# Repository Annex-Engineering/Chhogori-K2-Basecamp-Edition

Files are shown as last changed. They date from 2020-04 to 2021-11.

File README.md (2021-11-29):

# Notes:
as of 11-29-2021, K2 Basecamp edition will no longer recieve updates, this was voted upon by the community. We will do our best to make sure all frames are forwards compatible with any XY or Z axis related changes, however, we cannot guarantee anything.
 - Trails

# Chhogori (K2) Printer - Basecamp Edition - Release 2.1

Chhogori (K2) - Basecamp Edition: is a Medium Format, Direct Drive, Open Air FDM Printer.

This is an entirely scratch design, based on the efforts of the "Hypercube Overkill Project" for the XY Motion System

Our discord server can be found here: https://discord.gg/MzTR3zE

BOM/Sourcing Guide for a 250x250x250 Build can be found here: https://docs.google.com/spreadsheets/d/1O3eyVuQ6M4F03MJSDs4Z71_XyNjXL5HFTZr1jsaAtRc/edit?usp=sharing

Frame Calculator: https://docs.google.com/spreadsheets/d/13liXa9Ag0wGGfv0r0511OmAwZuGD7cvcuc0zpDakIw4/edit?usp=sharing

# Stats:
- Open Air Design
- 2020, and 2040 Frame Members
- Build Volumes of ~250^3 to 500^3 (use of whole plate available) + additional area to purge and wipe
     - Z can theoretically be 1m tall, just not fully supported or tested

- Direct Drive Extruder (Sherpa Mini or Ascender)

- Shortest Belt Paths Possible, 4 Motors, 2 Per X, 2 Per Y Axis
- Moving Bed, Fixed Gantry

- MGN12C Rails for XYZ Stationary Rails
- MGN12C Rails with 1515 Backers for XY Cross (Moving Members)
- 12mm 2GT Belts on XY Motion 
- 12mm 2GT Belts with 20 or 40:1 Worm Drive on Z to lift the Bed 
	 - Hybrid Laser Cut Metal and Printed Part Construction
	 - Legacy Support for 15mm 3HTD belts also offered
- Heavy Duty Bearings
- NEMA17 Motors XYZ

- Minimal Printed Parts (ABS or ASA Required)

- Fysetc Spider or S6 Controller + BTT Expander Board with Klipper Required
- Mosquito Style, Dragon Style, Mosquito Magnum+ and Nitram's VolcoMosquito hotends supported
- 24V Power Standard
- Mains Bed

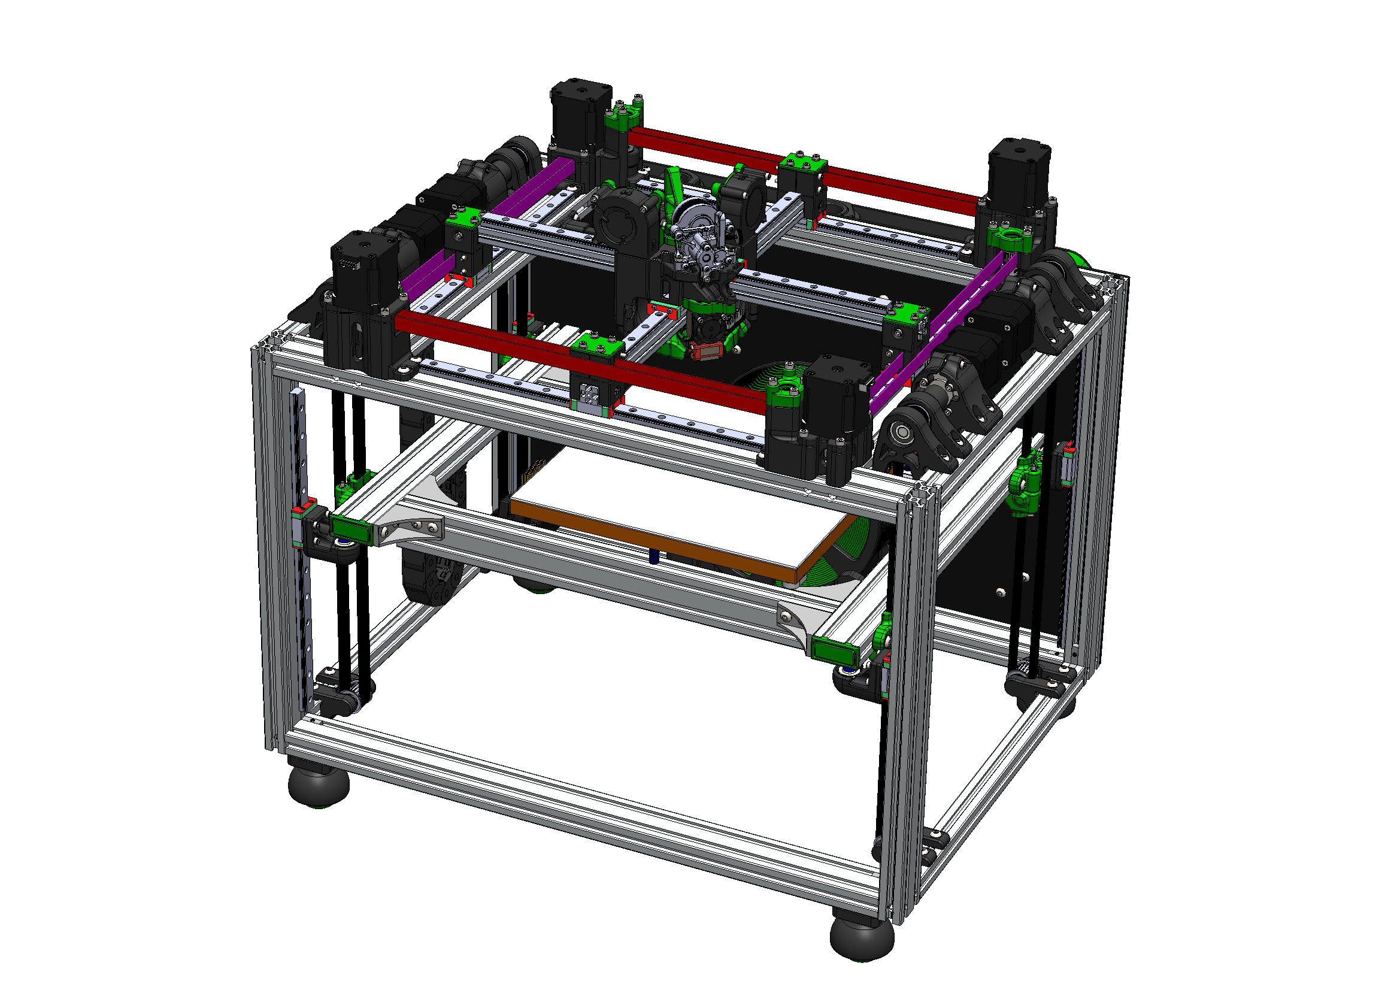
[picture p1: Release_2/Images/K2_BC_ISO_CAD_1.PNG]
Image of Machine with Panels


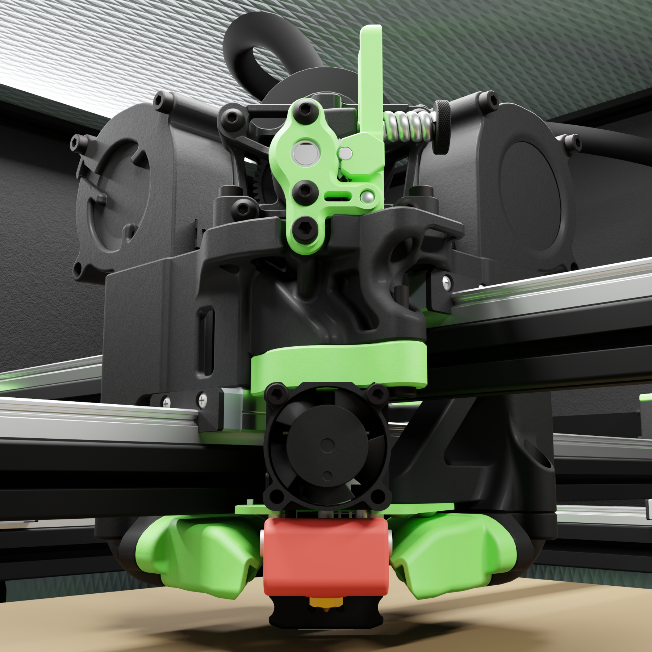
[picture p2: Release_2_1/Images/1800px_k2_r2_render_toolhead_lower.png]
Image of Toolhead 1


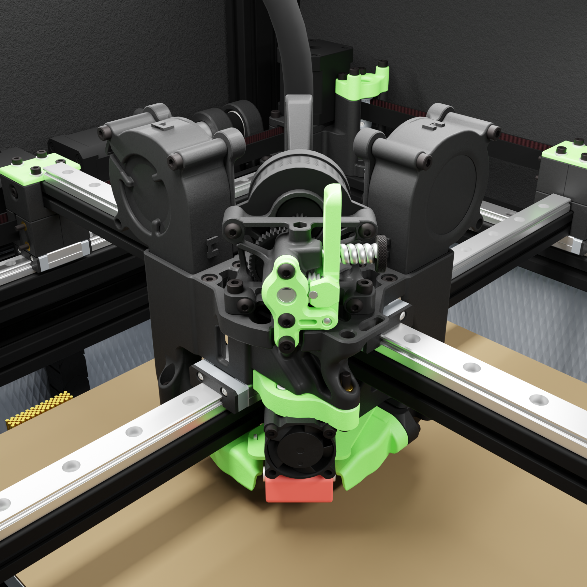
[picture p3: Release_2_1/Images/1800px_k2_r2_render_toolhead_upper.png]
Image of Toolhead 2


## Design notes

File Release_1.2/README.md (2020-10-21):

# Chhogori (K2) Printer - Basecamp Edition

These parts are purely pre-release at this point, please use with caution.

Use tab 2 on the frame calculator if you would like to build to this revision, please use discord for support

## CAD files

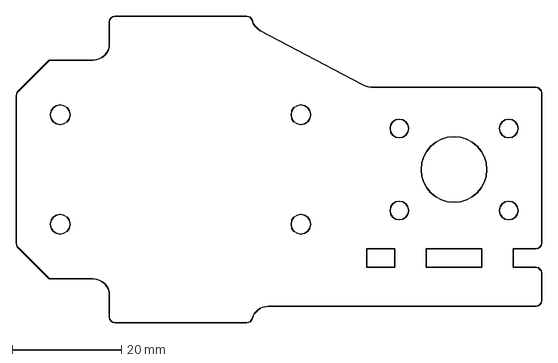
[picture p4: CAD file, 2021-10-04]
Release_2_1/DXFs/15mm_3HTD_Belted_Z_Drive/3mm_stainless_z_bearing_block_main_plate_x4_rev1.DXF
96.0 x 56.0 mm

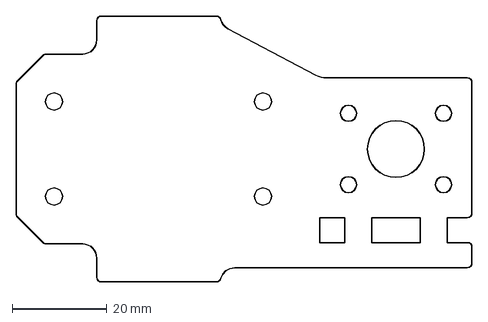
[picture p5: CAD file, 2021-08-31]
Release_2_1/DXFs/15mm_3HTD_Belted_Z_Drive/4.8mm_aluminum_z_bearing_block_main_plate_x4_rev1.DXF
96.0 x 56.0 mm

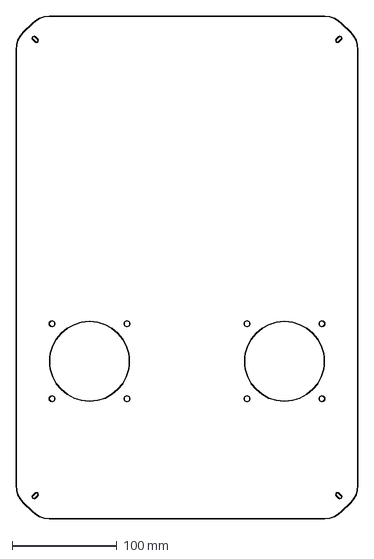
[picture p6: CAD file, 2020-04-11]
DXFs/Electronics_Box/electronics_box_cover_x1_rev1.DXF
326.0 x 479.0 mm

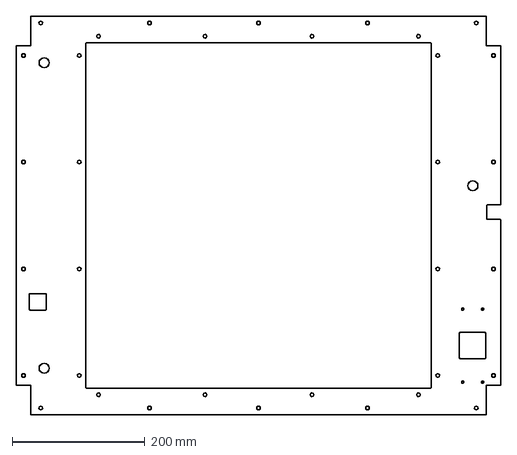
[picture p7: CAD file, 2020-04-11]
DXFs/Panels/Gantry_Deck_Panel_400mm_x_400mm_Rev1.DXF
730.0 x 600.0 mm

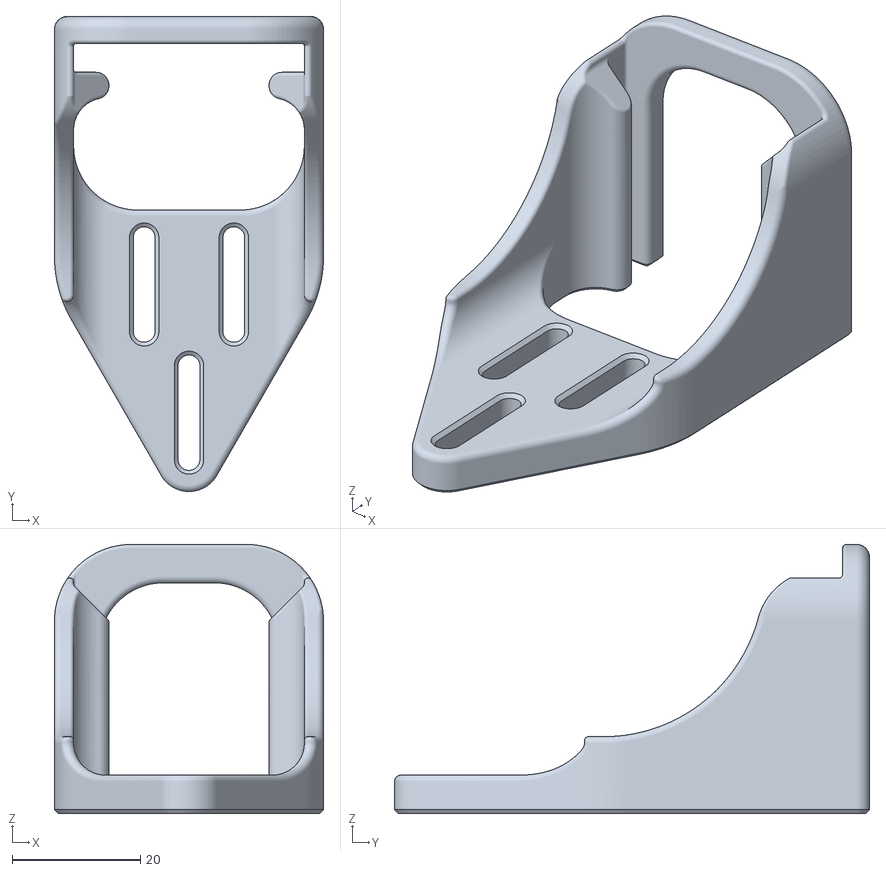
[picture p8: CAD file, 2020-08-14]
Release_1.2/STLs/Mesh_Bed_Probe/Magnetic_Probe/magnetic_probe_dock_x1_rev5.STL
42.0 x 74.1 x 42.0

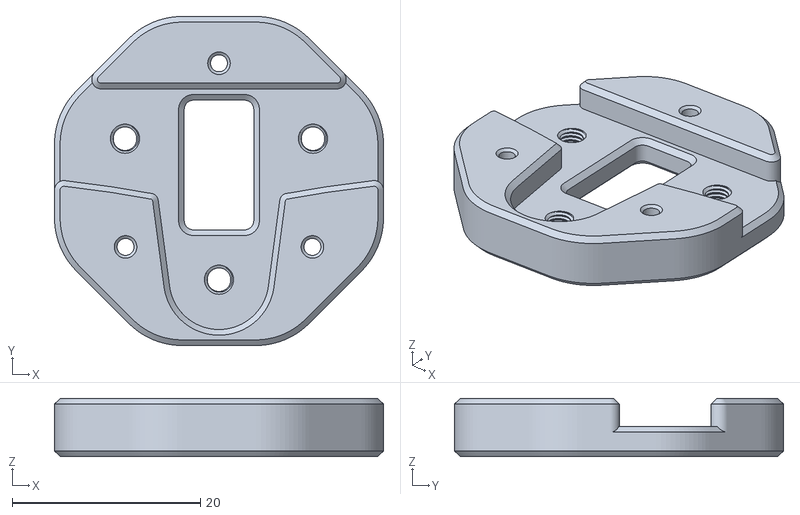
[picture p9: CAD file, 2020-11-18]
Release_1.2/STLs/Mesh_Bed_Probe/Piton_Probe/[a]_piton_probe_plate_6x3_x1_rev2.STL
35.0 x 35.0 x 6.20

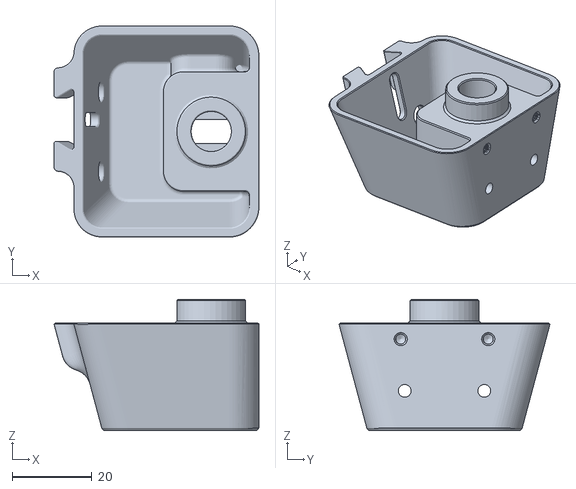
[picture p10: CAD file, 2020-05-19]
Release_1.2/STLs/Misc/z_endstop_housing_x1_rev1.STL
51.5 x 53.1 x 33.0

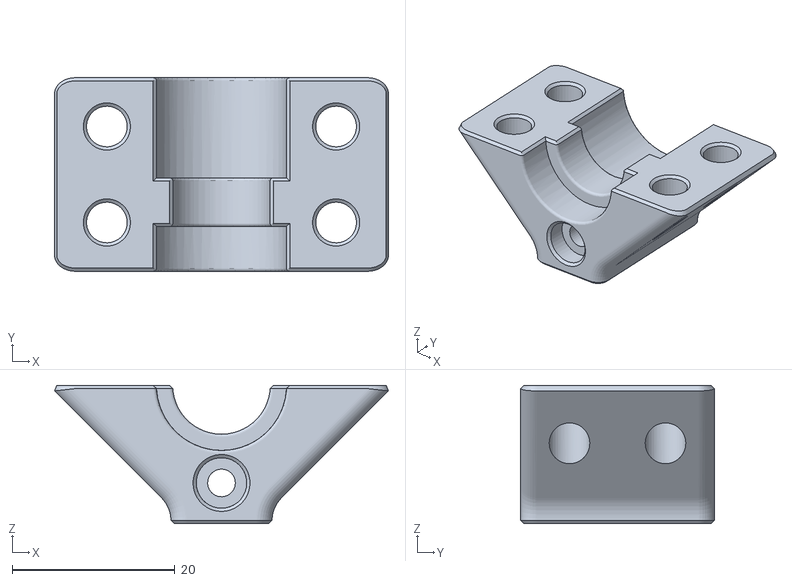
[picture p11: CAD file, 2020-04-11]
Release_1.2/STLs/XY_Carriage/Tool_Mounts/xy_carriage_v6_tool_mount_2_x1_rev3.STL
41.1 x 23.8 x 17.0

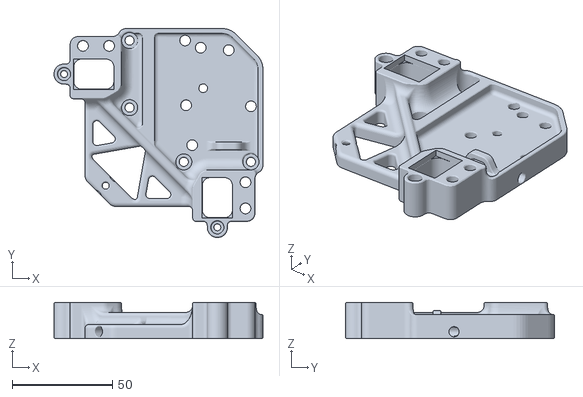
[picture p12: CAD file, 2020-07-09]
Release_1.2/STLs/XY_Carriage/Top_Plates/sherpa_tall_xy_carriage_top_plate_x1_rev1.STL
104.0 x 104.0 x 18.0

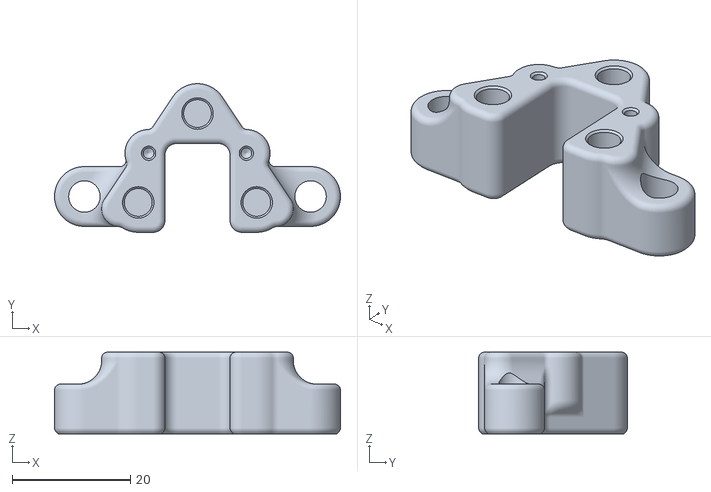
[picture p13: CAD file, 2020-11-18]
Release_1.2/STLs/XY_Carriage/xy_carriage_piton_probe_holder_mosquito_x1_rev3.STL
48.3 x 25.1 x 13.8

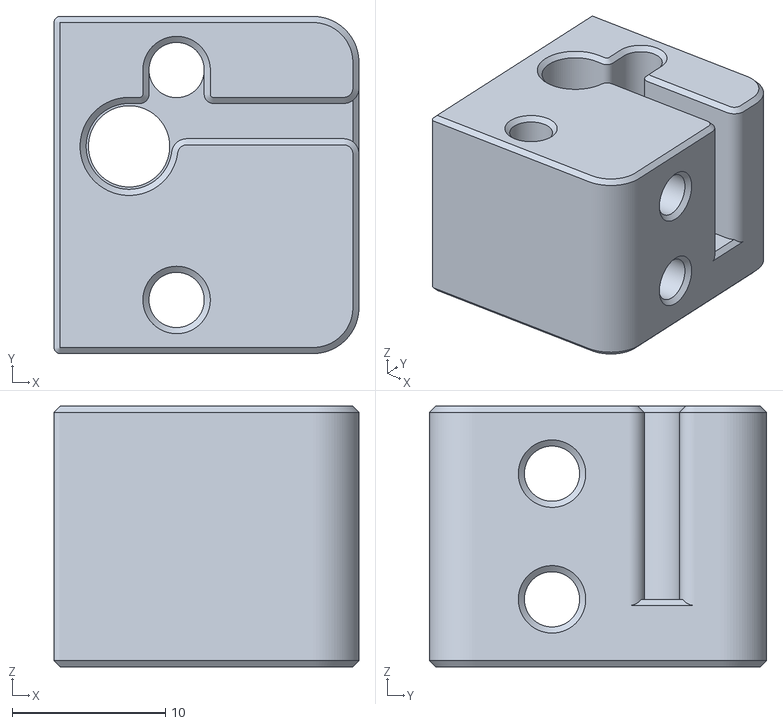
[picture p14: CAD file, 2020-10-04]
Release_1.2/STLs/XY_Gantry/xy_tensioner_left_20t_drive_x4_rev3.STL
19.9 x 22.0 x 17.0

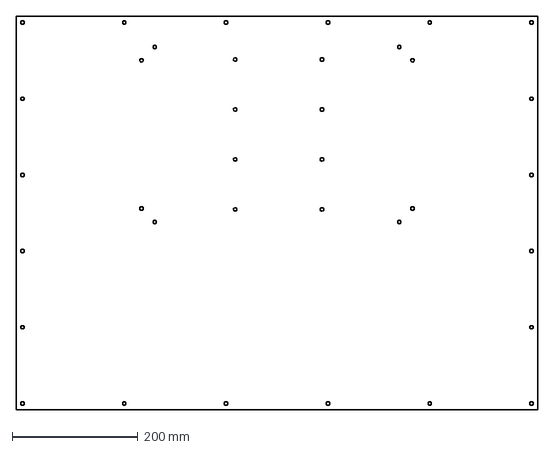
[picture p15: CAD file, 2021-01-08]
Release_2/DXFs/Panels/Back_Panel_500mm_x_500mm_Rev1.DXF
830.0 x 626.0 mm

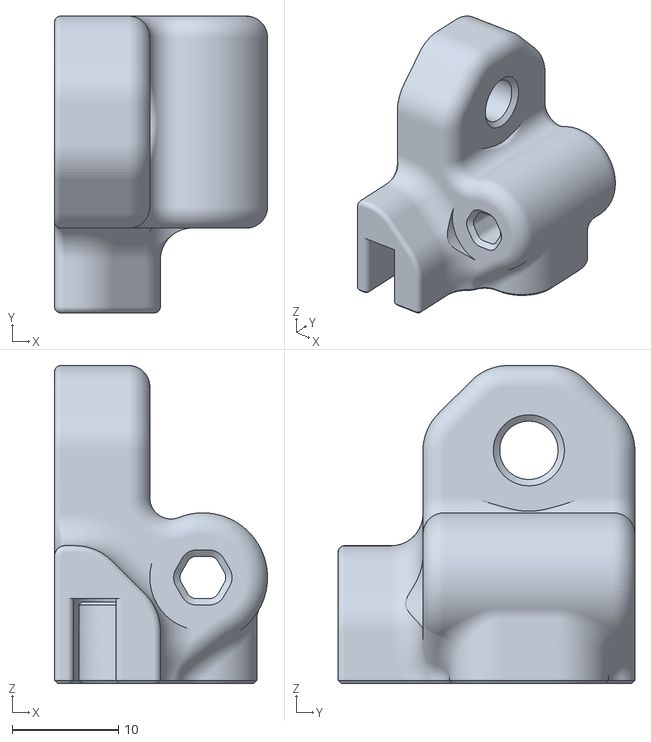
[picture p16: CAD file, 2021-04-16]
Release_2/STLs/Belted_Z_Drive/[a]_belted_z_tensioner_b1_x4_rev4.STL
20.1 x 28.0 x 30.0

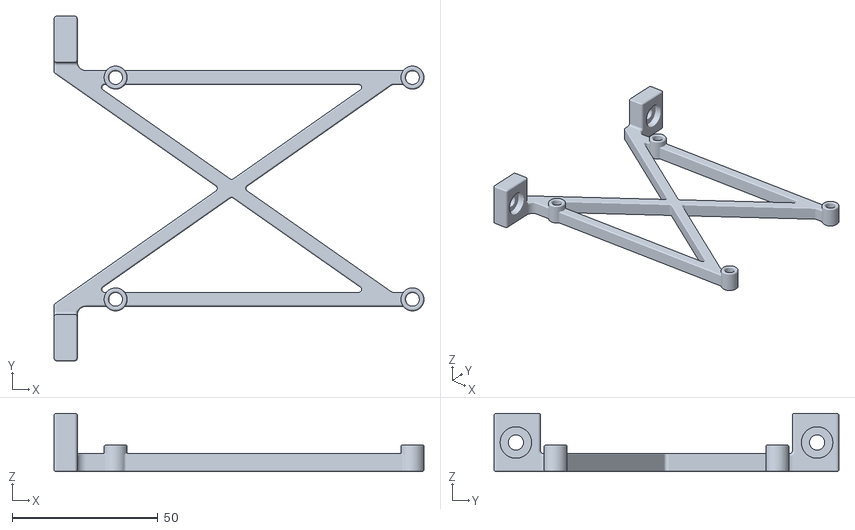
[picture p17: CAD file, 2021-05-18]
Release_2/STLs/Electronics_Brackets/bigtreetech_skr_mounting_bracket_x2_rev4.STL
127.0 x 118.3 x 20.0

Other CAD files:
Release_2_0_1/STLs/Belted_Z_Drive/[a]_belted_z_tensioner_a2_x4_rev4.STL
Release_2_0_1/STLs/Electronics_Brackets/raspberrypi_mounting_bracket_for_heatsink_vertical_x1_rev2.STL
Release_2_0_1/STLs/Jigs_and_Fixtures/[a]_mgn15_altz_rail_alignment_tool_x3_rev1.STL
Release_2_1/DXFs/12mm_2GT_Belted_Z_Drive/3mm_stainless_belted_worm_z_metal_top_40+20to1_x4_rev1.DXF
Archive/Release_1.2/CAD/BASS_Fan_Ducts.x_t
Archive/Release_1.2/CAD/FYSETC_S6_Mounting_Frame.x_t
Archive/Release_1.2/CAD/Piton_Probe_Assembly_11-18-2020.x_t
Archive/Release_1.2/DXFs/Electronics_Box/electronics_box_bottom_panel_TE_power_inlet_x1_rev2.DXF
Archive/Release_1.2/DXFs/Panels/Back_Panel_250mm_x_250mm_Rev1.DXF
Archive/Release_1.2/DXFs/Panels/Back_Panel_300mm_x_300mm_Rev1.DXF
Archive/Release_1.2/DXFs/Panels/Back_Panel_350mm_x_250mm_Rev1.DXF
Archive/Release_1.2/DXFs/Panels/Back_Panel_350mm_x_350mm_Rev1.DXF
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

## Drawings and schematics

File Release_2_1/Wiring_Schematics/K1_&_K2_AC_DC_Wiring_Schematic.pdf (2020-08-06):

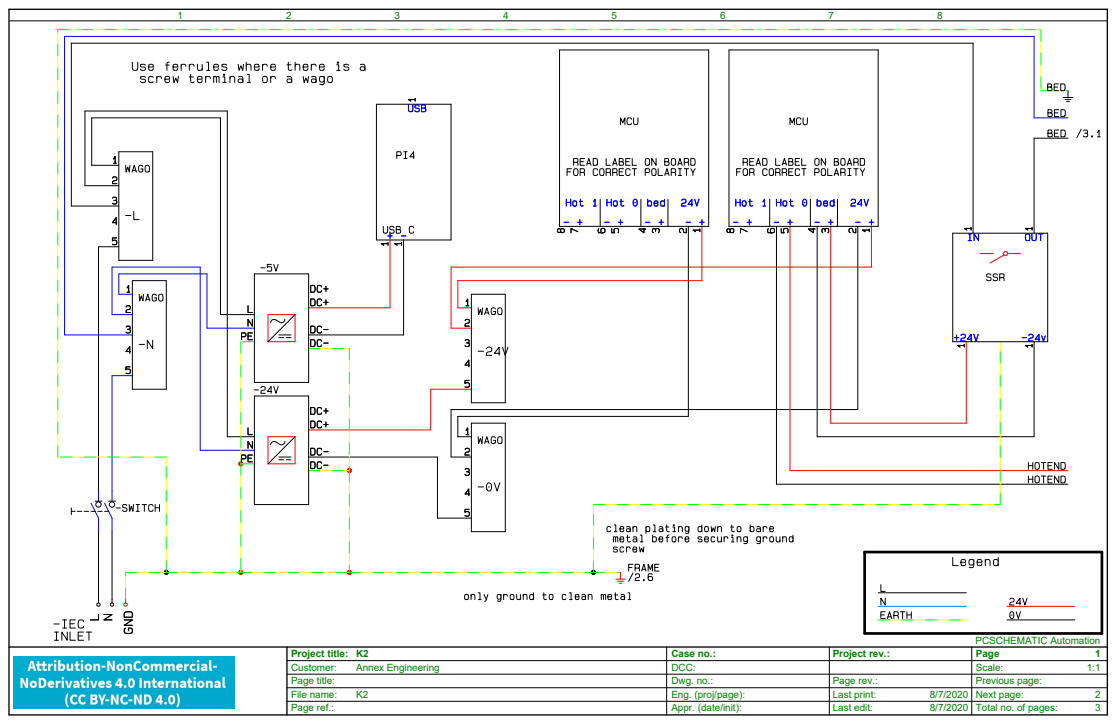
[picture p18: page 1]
PCSCHEMATIC Automation

Project title: K2 | Case no.: | Project rev.: | Page 1
Customer: Annex Engineering | DCC: | | Scale: 1:1
Page title: | Dwg. no.: | Page rev.: | Previous page:
File name: K2 | Eng. (proj/page): | Last print: 8/7/2020 | Next page: 2
Page ref.: | Appr. (date/init): | Last edit: 8/7/2020 | Total no. of pages: 3

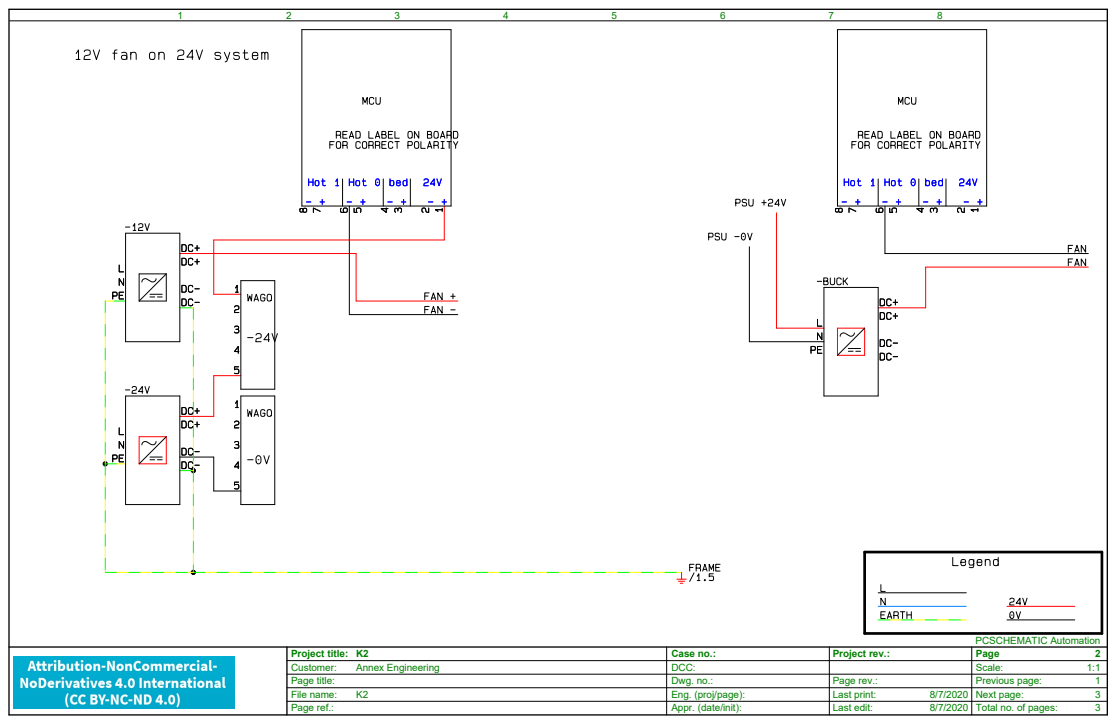
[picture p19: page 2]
PCSCHEMATIC Automation

Project title: K2 | Case no.: | Project rev.: | Page 2
Customer: Annex Engineering | DCC: | | Scale: 1:1

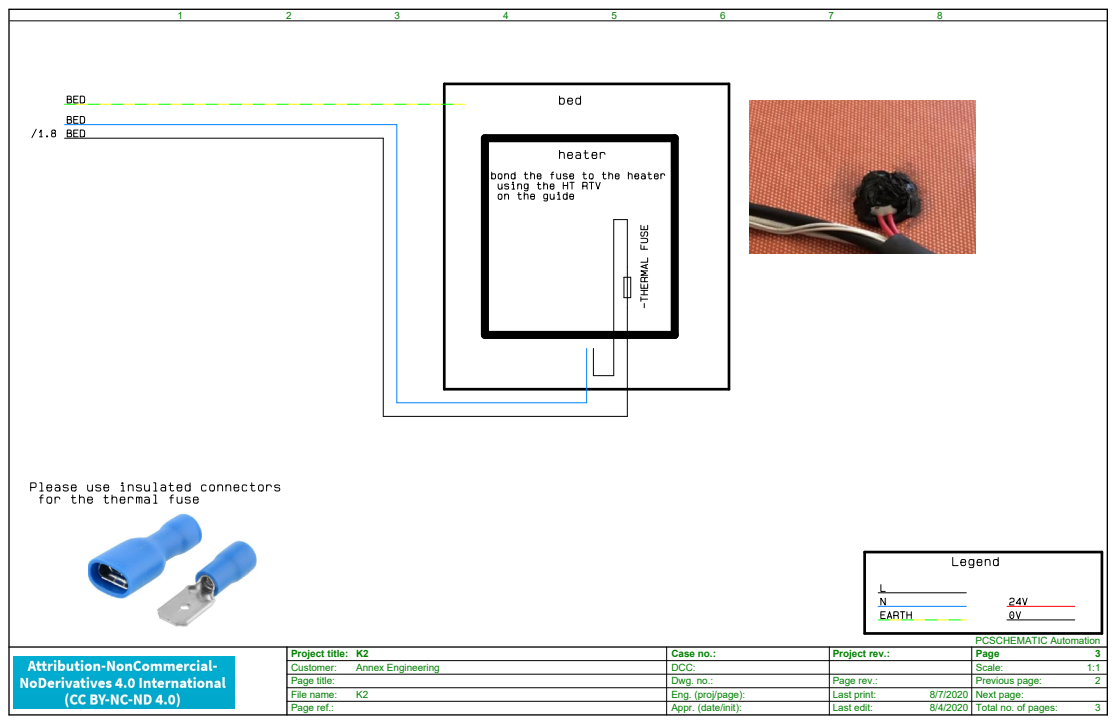
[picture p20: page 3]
PCSCHEMATIC Automation

Project title: K2 | Case no.: | Project rev.: | Page 3
Customer: Annex Engineering | DCC: | | Scale: 1:1

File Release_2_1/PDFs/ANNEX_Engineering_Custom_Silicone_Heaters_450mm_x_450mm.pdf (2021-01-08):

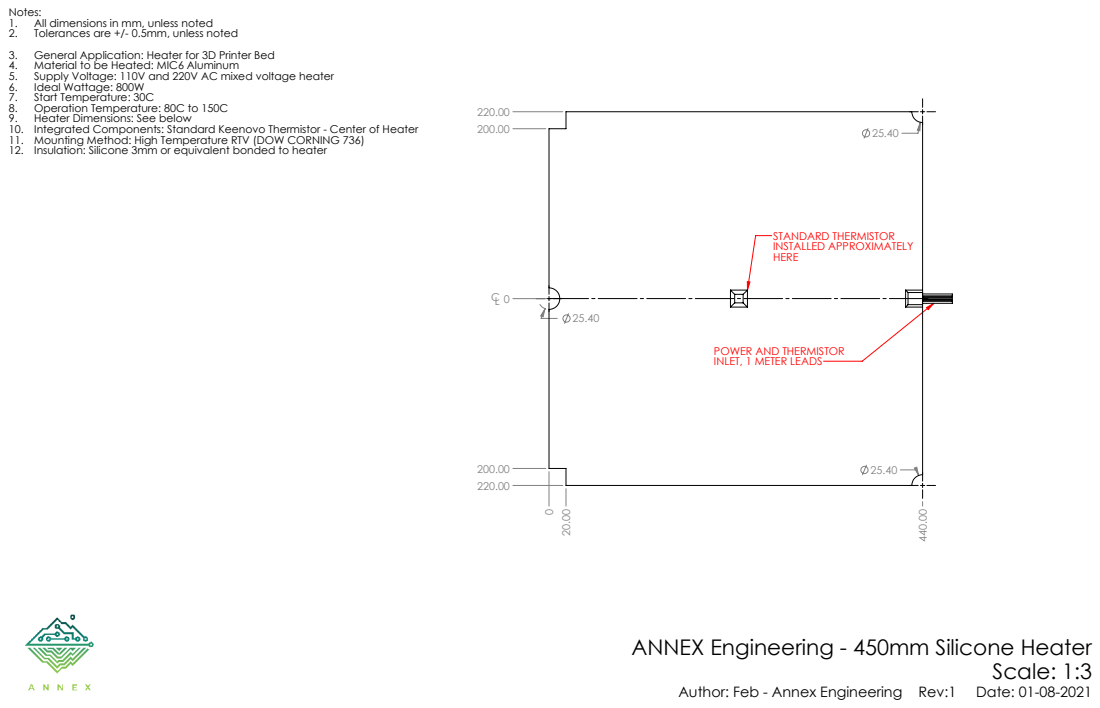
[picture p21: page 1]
STANDARD THERMISTOR INSTALLED APPROXIMATELY; Scale: 1:3

Notes:
1. All dimensions in mm, unless noted
2. Tolerances are +/- 0.5mm, unless noted
3. General Application: Heater for 3D Printer Bed
4. Material to be Heated: MIC6 Aluminum
5. Supply Voltage: 110V and 220V AC mixed voltage heater
6. Ideal Wattage: 800W
7. Start Temperature: 30C
8. Operation Temperature: 80C to 150C
9. Heater Dimensions: See below
10. Integrated Components: Standard Keenovo Thermistor - Center of Heater
11. Mounting Method: High Temperature RTV (DOW CORNING 736)
12. Insulation: Silicone 3mm or equivalent bonded to heater

POWER AND THERMISTOR
INLET, 1 METER LEADS

ANNEX Engineering - 450mm Silicone Heater

Author: Feb - Annex Engineering Rev:1 Date: 01-08-2021

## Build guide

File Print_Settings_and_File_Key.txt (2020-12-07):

Primary Color: nothing at start of file name
Accent Color: [a]_ at start of file name
Quantity Required: _x# near end of file name
File Revision: _Rev# at end of file name

Nozzle Size: 0.6mm Recommended
Recommended FDM Materials: ASA, Polymaker or 3DXTech Recommended
Alternate Approved FDM Materials: ABS, ABS+, 3DXtech or Atomic Filaments Recommended
Layer Height: 0.2mm or 0.3mm
Extrusion Width: Forced 0.6mm
Infill Percentage: 40% minimum (at 0.8mm Width)
Infill Type: Grid, Gyroid, Honeycomb, Triangle or Cubic
Wall Count: 3 minimum (at 0.6mm Width)
Solid Top/Bottom Layers: 5 minimum (at 0.2mm Height)

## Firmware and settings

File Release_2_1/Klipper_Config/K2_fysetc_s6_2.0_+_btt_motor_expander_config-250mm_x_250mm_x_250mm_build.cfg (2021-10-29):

# This file has been created by Trails, of Annex Engineering, for the K2 3D Printer.
# Please change settings for your specific build or ensure you place your items in the same spots on the same MCU as I have.
# I've added as many options as I can think of for different displays as well as listed the available commands you can use via the terminal at the bottom of this configuration file.

#THIS CONFIG IS FOR A 250mm x 250mm x 250mm K1 PRINTER ONLY FOR THE FYSETC S6 2.0 CONTROLLER with a BTT Motor Expander Connected to the display ports
#PLEASE READ THE WHOLE CONFIG BEFORE ATTEMPTING TO DO ANYTHING
#CONNECTORS/PORTS ON THE CONTROLLERS ARE NOTED WITH COMMENTS FOR EACH LOCATION/INPUT/OUTPUT

# use the following modifiers before the pin definition (ex: ^!ar99)
# ! 			invert the logic
# ^ 			activate 5v pullup (does not apply to all pins)
# mcu_name: 	use pins on additional MCU (ex: z:ar10)


# MCU S6
[mcu] 
	#You will need to set this definition manually following the instructions in the line below
#	obtain definition by "ls -l /dev/serial/by-id/" then unplug to verify
serial: /dev/serial/by-id/usb-Klipper_Klipper_firmware_12345-if00
restart_method: command

# EXP1 / EXP2 (display) pins
[board_pins]
aliases:
    # EXP1 header
    EXP1_1=PC9, EXP1_2=PA8,
    EXP1_3=PC11, EXP1_4=PD2,
    EXP1_5=PC10, EXP1_6=PC12,    # Slot in the socket on this side
    EXP1_7=PD0, EXP1_8=PD1,
    EXP1_9=<GND>, EXP1_10=<5V>,

    # EXP2 header
    EXP2_1=PA6, EXP2_2=PA5,
    EXP2_3=PC6, EXP2_4=PA4,
    EXP2_5=PC7, EXP2_6=PA7,      # Slot in the socket on this side
    EXP2_7=PB10, EXP2_8=<RST>,
    EXP2_9=<GND>, EXP2_10=<5V>


#virtual sdcard settings
[virtual_sdcard]
path: ~/gcode_files

#enable display status for moonraker
[display_status]

# Enable Pause/Resume Functionality
[pause_resume]

#Printer Speeds and Accels
[printer]
kinematics: cartesian
max_velocity: 350 #change this to 500 after comissioning
max_accel: 2000 #change this to 7500 after commissioning
max_z_velocity: 8 #change this to 15 after comissioning
max_z_accel: 500 #change this to 1000 after comissioning
square_corner_velocity: 5.0

#Gcode G2/G3 Arc Support
[gcode_arcs]
resolution: 0.1

#Input Shaper Settings
# you need to tune your printer for this, if your lazy you can use these values as a starting point
# [input_shaper]
# shaper_freq_x: 59 #(100*8)/13.5
# shaper_freq_y: 51 #(100*8)/15.75
# shaper_type: mzv


# Stepper Configs
[stepper_x]
# connected to X Stepper on S6
step_pin: PE11
dir_pin: PE10
enable_pin: !PE9
# 20t Pulley, 2mm Pitch on a 0.9deg Motor
rotation_distance: 40
microsteps: 16
full_steps_per_rotation: 400
# connected to virtual endstop
endstop_pin: tmc2209_stepper_x:virtual_endstop 
position_min: 0
position_endstop: 0
position_max: 260
homing_retract_dist: 0
homing_speed: 50.0
homing_positive_dir: false

[stepper_x1]
# connected to Y Stepper on S6
step_pin: PD8
dir_pin: !PB12
enable_pin: !PD9
# 20t Pulley, 2mm Pitch on a 0.9deg Motor
rotation_distance: 40
microsteps: 16
full_steps_per_rotation: 400
# connected to virtual endstop
endstop_pin: tmc2209_stepper_x1:virtual_endstop 



[stepper_y]
# connected to E0 Stepper on S6
step_pin: PD5
dir_pin: PD6
enable_pin: !PD4
# 20t Pulley, 2mm Pitch on a 0.9deg Motor
rotation_distance: 40
microsteps: 16
full_steps_per_rotation: 400
# connected to virtual endstop
endstop_pin: tmc2209_stepper_y:virtual_endstop 
position_min: 0
position_endstop: 0
position_max: 260
homing_retract_dist: 0
homing_speed: 50.0
homing_positive_dir: false

[stepper_y1]
# connected to E1 Stepper on S6
step_pin: PE6
dir_pin: !PC13
enable_pin: !PE5
# 20t Pulley, 2mm Pitch on a 0.9deg Motor
rotation_distance: 40
microsteps: 16
full_steps_per_rotation: 400
# connected to virtual endstop
endstop_pin: tmc2209_stepper_y1:virtual_endstop 



[stepper_z]
# connected to Stepper 1 on BTT Motor Expander (Front Left Stepper, from top)
step_pin: EXP2_6
dir_pin: !EXP2_5
enable_pin: !EXP2_7

# 20t Pulley, 2mm Pitch on a 1.8deg Motor with a 40:1 worm drive attached
rotation_distance: 40
microsteps: 4
full_steps_per_rotation: 200
gear_ratio: 40:1

# connected to Z- Endstop on S6
endstop_pin: probe:z_virtual_endstop
position_max: 220 #this is set here on purpose, your actual travel will vary based on spring compression holding the bed, adjust at your own risk
position_min: -5
homing_speed: 10.0
second_homing_speed: 5.0
homing_retract_dist: 15.0
homing_positive_dir: false
 
[stepper_z1]
# connected to Stepper 2 on BTT Motor Expander (Rear Left Stepper, from top)
step_pin: EXP2_3
dir_pin: !EXP2_4
enable_pin: !EXP1_8

# 20t Pulley, 2mm Pitch on a 1.8deg Motor with a 40:1 worm drive attached
rotation_distance: 40
microsteps: 4
full_steps_per_rotation: 200
gear_ratio: 40:1
 
[stepper_z2]
# connected to Stepper 3 on BTT Motor Expander (Rear Right Stepper, from top)
step_pin: EXP2_1
dir_pin: !EXP2_2
enable_pin: !EXP1_7

# 20t Pulley, 2mm Pitch on a 1.8deg Motor with a 40:1 worm drive attached
rotation_distance: 40
microsteps: 4
full_steps_per_rotation: 200
gear_ratio: 40:1

[stepper_z3]
# connected to E2 Stepper on S6 (Front Right Stepper, from top)
step_pin: PE2
dir_pin: !PE4
enable_pin: !PE3

# 20t Pulley, 2mm Pitch on a 1.8deg Motor with a 40:1 worm drive attached
rotation_distance: 40
microsteps: 4
full_steps_per_rotation: 200
gear_ratio: 40:1



# TMC Stepper Configurations for All Motors
[tmc2209 stepper_x]
# connected to X Stepper on S6
uart_pin: PE8
interpolate: true
run_current: 1.0 
sense_resistor: 0.110
stealthchop_threshold: 0
# Place a jumper on the two pin header near the endstop for sensorless homing
diag_pin: PB14 #connected to X- Endstop (X Jumper Header)
driver_SGTHRS: 115

[tmc2209 stepper_x1]
# connected to Y Stepper on S6
uart_pin: PC4
interpolate: true
run_current: 1.0 
sense_resistor: 0.110
stealthchop_threshold: 0
# Place a jumper on the two pin header near the endstop for sensorless homing
diag_pin: PB13 #connected to Y- Endstop (Y Jumper Header)
driver_SGTHRS: 115

[tmc2209 stepper_y]
# connected to E0 Stepper on S6
uart_pin: PA15
interpolate: true
run_current: 1.0  
sense_resistor: 0.110
stealthchop_threshold: 0
# Place a jumper on the two pin header near the endstop for sensorless homing
diag_pin: PA3 #connected to Z+ Endstop (E0 Jumper Header)
driver_SGTHRS: 115

[tmc2209 stepper_y1]
# connected to E1 Stepper on S6
uart_pin: PC5
interpolate: true
run_current: 1.0 
sense_resistor: 0.110
stealthchop_threshold: 0
# Place a jumper on the two pin header near the endstop for sensorless homing
diag_pin: PA2 #connected to Y+ Endstop (E1 Jumper Header)
driver_SGTHRS: 115
 
[tmc2209 stepper_z]
# connected to Stepper 1 on BTT Motor Expander (Front Left Stepper, from top)
uart_pin: EXP1_6
interpolate: true
run_current: 1.2
hold_current: 1.0 
sense_resistor: 0.110
stealthchop_threshold: 0

[tmc2209 stepper_z1]
# connected to Stepper 2 on BTT Motor Expander (Rear Left Stepper, from top)
uart_pin: EXP1_4
interpolate: true
run_current: 1.2
hold_current: 1.0 
sense_resistor: 0.110
stealthchop_threshold: 0

[tmc2209 stepper_z2]
# connected to Stepper 3 on BTT Motor Expander (Rear Right Stepper, from top)
uart_pin: EXP1_2
interpolate: true
run_current: 1.2
hold_current: 1.0
sense_resistor: 0.110
stealthchop_threshold: 0

[tmc2209 stepper_z3]
# connected to E2 Stepper on S6 (Front Right Stepper, from top)
uart_pin: PE0
interpolate: true
run_current: 1.2
hold_current: 1.0
sense_resistor: 0.110
stealthchop_threshold: 0

[tmc2209 extruder]
# connected to Z Stepper on S6 
uart_pin: PD12
interpolate: false
run_current: 0.3
sense_resistor: 0.110
stealthchop_threshold: 0


# Force Move
	used to force a single stepper to move.  not used once setup
[force_move]
enable_force_move: true


# Dockable Probe
[dockable_probe]
# connected to Z- Endstop on S6
pin: PA0
x_offset: -12.5 # offset for microswitch x direction off nozzle
y_offset: 16 # offset for microswitch y direction off nozzle
z_offset: 8 # offset for microswitch in z height - this is a starting point only
samples: 3
sample_retract_dist: 15
samples_result: median
samples_tolerance: 0.02
samples_tolerance_retries: 3
speed: 3
lift_speed: 10

# dockable probe specific
dock_position:             2,258, 20 #back left corner of gantry
safe_z_position:           125,125 #center of bed
approach_position:		   32,228
detach_position:		   77, 258
attach_speed:              20
detach_speed:              100
travel_speed:              300
check_open_attach:         True
dock_fixed_z:              True
dock_retries:			   1

#   Optional custom gcode sections for dockable probe
pre_attach_gcode:
    G1 X40 Y40 F18000    #keep umbilical from catching on stuff
pre_detach_gcode:
    G1 X40 Y40 F18000   #keep umbilical from catching on stuff
post_detach_gcode:
	G1 X125 Y125 F18000  #keep gantry from murdering itself after docking probe
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

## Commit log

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2020-04-12 refactor xy carriage, add lightness and air
    refactor xy carriage, add lightness and air
    [[a]_xy_carriage_fan_duct_1_x1_rev6.STL, [a]_xy_carriage_fan_duct_1_x1_rev7.STL, [a]_xy_carriage_fan_duct_2_x1_rev6.stl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]
2020-04-14 remove duet toolboard mount, tweak length and clearance on cable anchor on x carriage, add magnet removal holes to probe pickup
    [[a]_duet3_toolboard_holder_x1_rev2.STL, xy_carriage_cable_anchor_x1_rev1.STL, xy_carriage_cable_anchor_x1_rev2.STL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]
2020-04-15 z_tilt typo, fix
    [K2_bigtree_skr_1.3_config-250mm_x_250mm_x_250mm_build.cfg]
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2020-04-16 correct minor dimensional typo in deck plates
    [Gantry_Deck_Panel_250mm_x_250mm_Rev2.DXF, Gantry_Deck_Panel_300mm_x_300mm_Rev2.DXF, Gantry_Deck_Panel_350mm_x_350mm_Rev2.DXF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]
2020-04-16 stiffen bmg mounting bracket
    [bmg_mounting_bracket_x1_rev1.STL, bmg_mounting_bracket_x1_rev2.STL]
2020-04-18 fix non-manifold parts
    fix non-manifold parts
    [[a]_xy_carriage_fan_duct_2_x1_rev7.stl]
2020-04-19 dual xy switch drive tower support
    dual xy switch drive tower support
    [[a]_bearing_cap_x4_rev4.STL, [a]_bearing_cap_x4_rev5.STL, short_motor_tall_idler_mount_x2_rev2.STL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]
2020-04-19 xy tower idlers use same bolt length for all 4 bolts, update edrawing
    xy tower idlers use same bolt length for all 4 bolts, update edrawing
    [[a]_bearing_cap_x4_rev5.STL, [a]_short_motor_tall_idler_bearing_cap_x2_rev1.STL, [a]_tall_motor_short_idler_bearing_cap_x2_rev1.STL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]
2020-04-19 fix dimensional typo on back panel dxf
    [electronics_box_cover_x1_rev2.DXF]
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2020-04-22 z ballscrew+rail block from heatset inserts to thru bolts and nylon lock nuts
    z ballscrew+rail block from heatset inserts to thru bolts and nylon lock nuts
    [z_bearing_block_b_mirror_x2_rev2.STL, z_bearing_block_b_mirror_x2_rev3.STL, z_bearing_block_b_x1_rev2.stl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]
2020-04-22 replace z rail alignment tool with correct one, tighten tolerances on rail alignment tools
    replace z rail alignment tool with correct one, tighten tolerances on rail alignment tools
    [[a]_mgn9_3rd_z_rail_install_tool_x3_rev1.stl, [a]_mgn9_3rd_z_rail_install_tool_x3_rev2.stl, [a]_mgn9_rail_install_tool_2060_x3_rev1.STL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]
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2020-04-25 add experimental 16t drive/idler pulley support
    add experimental 16t drive/idler pulley support
    [xy_tensioner_left_16t_drive_x4_rev1.STL, xy_tensioner_left_20t_drive_x4_rev2.STL, xy_tensioner_right_16t_drive_x4_rev1.STL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]
2020-04-27 M4 heatset inserts were too tight on install, short tower M3 screw clearance hole for motor to base was too small (3.3 vs 3.6)
    M4 heatset inserts were too tight on install, short tower M3 screw clearance hole for motor to base was too small (3.3 vs 3.6)
    [motor_idler_top_plate_x4_rev1.STL, short_motor_tall_idler_mount_x2_rev4.STL, short_motor_tall_idler_mount_x2_rev5.STL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]
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2020-05-06 z chain anchors were missing from stl folder
    [bed_wiring_retaining_clip_x2_rev1.STL, z_chain_anchor_bottom_x1_rev1.STL, z_chain_anchor_top_x1_rev1.STL]
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2020-05-31 update xy carriage top plate to restore full xy travel, stiffen part by 15%
    [bmg_xy_carriage_top_plate_x1_rev2.STL, bmg_xy_carriage_top_plate_x1_rev3.STL]
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2020-07-05 idler tower beefup, update edrawings
    fix extremely rare case where the xy idler top cap can split (aka 12k accel at 500mm/s for extended periods of time), by reducing stress points present and increasing radius sizes in weaker regions.
    [[a]_short_motor_tall_idler_bearing_cap_x2_rev1.STL, [a]_short_motor_tall_idler_bearing_cap_x2_rev2.STL, [a]_tall_motor_short_idler_bearing_cap_x2_rev1.STL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]
2020-07-07 add reinforcing ribs to bmg top plate
    trying to stiffen tool mounting point in an effort to reduce low speed ringing
    [bmg_xy_carriage_top_plate_x1_rev3.STL, bmg_xy_carriage_top_plate_x1_rev4.STL]
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2020-07-28 reduce material use on controller and rs-25-5 bracket
    reduce material use on controller and rs-25-5 bracket
    [bigtreetech_skr_mounting_bracket_x2_rev2.STL, bigtreetech_skr_mounting_bracket_x2_rev3.STL, fysetc_s6_mounting_bracket_x2_rev2.STL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]
2020-07-28 add printed BF10 (bottom bearing) replacement block
    optional for now, requires 608 bearing
    [printed_BF10_block_alternative_x3_rev1.STL]
2020-07-28 fix stl orientation
    [printed_BF10_block_alternative_x3_rev1.STL]
2020-07-28 add high flow variant of ducting (for pla, etc)
    add high flow variant of ducting (for pla, etc)
    [[a]_xy_carriage_fan_duct_1_high_flow_x1_rev1.STL, [a]_xy_carriage_fan_duct_2_high_flow_x1_rev1.STL]
2020-07-29 revision 2 of high flow fan ducting
    revision 2 of high flow fan ducting
    [[a]_xy_carriage_fan_duct_1_high_flow_x1_rev1.STL, [a]_xy_carriage_fan_duct_1_high_flow_x1_rev2.STL, [a]_xy_carriage_fan_duct_2_high_flow_x1_rev1.STL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]
2020-07-29 Revert "revision 2 of high flow fan ducting"
    This reverts commit 6bcf16657015a92ed5c22a504174a78ed10e3d01.
    [[a]_xy_carriage_fan_duct_1_high_flow_x1_rev1.STL, [a]_xy_carriage_fan_duct_1_high_flow_x1_rev2.STL, [a]_xy_carriage_fan_duct_2_high_flow_x1_rev1.STL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]
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2020-07-31 add oldham coupler style joint to z axis
    reduces chances of bent screws (especially if your on a budget) of affecting print quality
    [z_bearing_block_a_mirror_oldham_x1_rev1.STL, z_bearing_block_a_oldham_x2_rev1.STL, z_bearing_block_a_x3_rev2.STL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]
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2020-08-04 high flow fan duct now standard
    high flow fan duct now standard
    [[a]_xy_carriage_fan_duct_1_high_flow_x1_rev1.STL, [a]_xy_carriage_fan_duct_1_high_flow_x1_rev2.STL, [a]_xy_carriage_fan_duct_1_x1_rev8.STL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]
2020-08-04 reduce material usage on probe dock
    reduce material usage on probe dock
    [magnetic_probe_dock_x1_rev3.STL, magnetic_probe_dock_x1_rev4.STL]
2020-08-06 oldham pockets werent set on layer multiples, move idler tower on xy 1mm forward for more motor clearance
    oldham pockets werent set on layer multiples, move idler tower on xy 1mm forward for more motor clearance
    [short_motor_tall_idler_mount_x2_rev6.STL, short_motor_tall_idler_mount_x2_rev7.STL, tall_motor_short_idler_mount_x2_rev6.STL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]
2020-08-06 minor oldham slot geometry adjustment for better printability
    minor oldham slot geometry adjustment for better printability
    [z_bearing_block_a_mirror_oldham_x1_rev2.STL, z_bearing_block_a_mirror_oldham_x1_rev3.STL, z_bearing_block_a_oldham_x2_rev2.STL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]
2020-08-06 prevent flat sections from appearing in oldham pockets
    prevent flat sections from appearing in oldham pockets
    [z_bearing_block_a_mirror_oldham_x1_rev3.STL, z_bearing_block_a_mirror_oldham_x1_rev4.STL, z_bearing_block_a_oldham_x2_rev3.STL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]
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2020-08-08 quantity on mirror and std was inverted
    quantity on mirror and std was inverted
    [z_bearing_block_a_mirror_oldham_x2_rev4.STL, z_bearing_block_a_oldham_x1_rev4.STL]
2020-08-13 add Meanwell LRS-200 and LRS-350 (and RSP) mounting bracket for converts from other machines
    add Meanwell LRS-200 and LRS-350 (and RSP) mounting bracket for converts from other machines
    [meanwell_lrs_200&350_24_psu_mounting_bracket_x2_rev1.STL]
2020-08-13 add sensorless homing, input shaper and bmg direct drive support to config
    [K2_bigtree_skr_1.3_config-250mm_x_250mm_x_250mm_build.cfg]
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2020-08-16 hollow out electronics box corner, reduce material and print time
    hollow out electronics box corner, reduce material and print time
    [[a]_electronics_box_corner_x4_rev2.STL, [a]_electronics_box_corner_x4_rev3.STL]
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2020-08-26 chain anchors had holes for m3 inserts, should be m4, simplify and add lightness
    chain anchors had holes for m3 inserts, should be m4, simplify and add lightness
    [z_chain_anchor_bottom_x1_rev2.STL, z_chain_anchor_bottom_x1_rev3.STL, z_chain_anchor_top_x1_rev2.STL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]
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2020-08-27 add fysetc s6 + btt motor expander bracket, update skr bracket to match
    add fysetc s6 + btt motor expander bracket, update skr bracket to match
    [bigtreetech_skr_mounting_bracket_with_motor_expander_x1_rev1.STL, bigtreetech_skr_mounting_bracket_with_motor_expander_x1_rev2.STL, fysetc_s6_mounting_bracket_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]
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2020-09-03 fix print orientation on part
2020-09-07 replace normal ascender top plate with folded ascender top plate
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2020-09-15 Update README.md
    Release Schedule:
    - Release 1 - RC2: Final True Release
    - Release 1: Bug Fixes from Final Testing of RC2
    - Release 1.1: Belted Z Drive Option
    - Release 1.2: New Front Door Design
    - Release 2.0: New Gantry
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2020-10-04 fix print orientation for parts
    [xy_tensioner_left_20t_drive_x4_rev3.STL, xy_tensioner_right_20t_drive_x4_rev5.STL]
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2020-10-19 add jigs and fixtures folder, add belted z install spacer
    [[a]_belted_z_install_jig_x1_rev1.STL, [a]_mgn9_3rd_z_rail_install_tool_x3_rev2.stl, [a]_mgn9_rail_install_tool_2060_x3_rev2.STL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]
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2020-10-22 add DXFs, PDFs and wiring schematic to release 1.1, remove deck plate, remove filament switch cluster
    removed parts are not compatible with belted z
    [Back_Panel_250mm_x_250mm_Rev1.DXF, Back_Panel_300mm_x_300mm_Rev1.DXF, Back_Panel_350mm_x_250mm_Rev1.DXF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]
2020-10-23 coupler needed additional clearance on drive tower
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2020-11-17 add alt z rail install tools, so rails can be installed with back panels on
    [[a]_mgn12_altz_rail_alignment_tool_x3_rev1.STL, [a]_mgn15_altz_rail_alignment_tool_x3_rev1.STL, [a]_mgn9_altz_rail_alignment_tool_x3_rev1.STL]
2020-11-18 add slicer profiles and belted z skr1.3 config to 1.2 beta
    add slicer profiles and belted z skr1.3 config to 1.2 beta
    [K2_bigtree_skr_1.3_config-250mm_x_250mm_x_250mm_build.cfg]
2020-11-18 replace 10x3 CS piton with 6x3 flat magnet piton
    [[a]_piton_probe_cap_6x3_x1_rev2.STL, [a]_piton_probe_plate_6x3_x1_rev2.STL, [a]_piton_probe_plate_x1_rev1.STL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]
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2020-11-18 add skr1.4 config, fix minor typos on 1.3 config, remove old 1.3 code
    [K2_bigtree_skr_1.4_config-250mm_x_250mm_x_250mm_build.cfg]
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2020-11-19 upload correct model of endcap
    [[a]_2040_extrusion_endcap_x2_rev1.STL, [a]_2040_extrusion_endcap_x2_rev2.STL]
2020-11-19 add s6 1.2 config, update comments and such in 1.3 and 1.4 configs, add blocks for belted z
    [K2_bigtree_skr_1.3_config-250mm_x_250mm_x_250mm_build.cfg, K2_fysetc_s6_1.2_config-250mm_x_250mm_x_250mm_build.cfg]
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2020-11-25 fix motor key flange interference in motor mounts
2020-11-26 fix print orientation
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2020-11-27 couldnt pass SHCS thru access holes, fixed that
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2020-12-04 add support for mgn12c rails on z ballscrew axis (22mm nuts only)
    [z_bearing_block_a_mirror_oldham_22mm_nut_mgn12c_x2_rev1.STL, z_bearing_block_a_mirror_oldham_22mm_nut_mgn9h_x2_rev4.STL, z_bearing_block_a_oldham_22mm_nut_mgn1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]
2020-12-06 wrong uart/tx on z3
    [K2_fysetc_s6_1.2_config-250mm_x_250mm_x_250mm_build.cfg]
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2020-12-09 add missing stls, pdfs and dxfs to r2 folder
    [BF10_block_x3_rev1.STL.STL, Back_Panel_250mm_x_250mm_Rev1.DXF, Back_Panel_300mm_x_300mm_Rev1.DXF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]
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2020-12-29 add fixed probe feb configs
    [k2_config_release2xy_3beltedz_fixed-probe.cfg, k2_config_release2xy_4beltedz_fixed-probe-mental.cfg, k2_config_release2xy_ballscrewz.cfg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]
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2020-12-31 uploaded wrong toolhead
2021-01-01 5020 fan pocket clearance
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2021-01-08 replace step_distance with rotation_distance on release 1.2 configs
    [K2_bigtree_skr_1.3_config-250mm_x_250mm_x_250mm_build.cfg, K2_bigtree_skr_1.4_config-250mm_x_250mm_x_250mm_build.cfg, K2_fysetc_s6_1.2_config-250mm_x_250mm_x_2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]
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2021-01-08 add microstepping and full steps per rotation sections to config, they were missed by mistake
    [K2_bigtree_skr_1.3_config-250mm_x_250mm_x_250mm_build.cfg, K2_bigtree_skr_1.4_config-250mm_x_250mm_x_250mm_build.cfg, K2_fysetc_s6_1.2_config-250mm_x_250mm_x_2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]
2021-01-08 add s6 2.0 config, fix pin issue on 1.2 config
    [K2_fysetc_s6_2.0_config-250mm_x_250mm_x_250mm_build.cfg]
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2021-01-19 add draft to probe dock and probe housing to aid in entry when dock is slightly misaligned
    [omron_d2f-5_microswitch_probe_body_x1_rev1.STL, omron_d2f-5_microswitch_probe_body_x1_rev2.STL]
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2021-01-22 dragon tool mount was 1mm too long, add 1st stage of new fan duct setup
    [[a]_xy_carriage_dragon_tool_mount_x1_rev4.STL, [a]_xy_carriage_dragon_tool_mount_x1_rev5.STL, xy_carriage_bottom_frame_magswitch_probe_v2_x1_rev3.STL]
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2021-03-03 belt retaining screw was 5.3mm insert hole, corrected to 4.7mm
    [xy_mgn12c_tensioner_left_20t_drive_12mm_belts_x4_rev1.STL, xy_mgn12c_tensioner_left_20t_drive_12mm_belts_x4_rev2.STL, xy_mgn12c_tensioner_right_20t_drive_12mm_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]
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2021-05-05 revised toolhead for more stability at 12k+ accels, more umbilical stability
    [[a]_carabiner_mounting_bracket_x1_rev1.STL, xy_carriage_bottom_frame_magswitch_probe_v2_x1_rev3.STL]
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2021-05-25 add extremely preliminary mag+ support (requires flipping the magswitch dock 180deg in the holder to work)
    [[a]_xy_carriage_mellow_mosquito_tool_mount_x1_rev1.STL, [a]_xy_carriage_std_fan_duct_1_x1_rev1.STL, [a]_xy_carriage_std_fan_duct_2_x1_rev1.STL]
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2021-05-29 shorten stack height of rpi bracket to better fit on k3 printers
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2021-05-30 bed mesh fade fix
    [K2_fysetc_s6_2.0_+_btt_motor_expander_config-250mm_x_250mm_x_250mm_build.cfg, K2_fysetc_s6_2.0_x2_config-250mm_x_250mm_x_250mm_build.cfg, K2_fysetc_spider_+_bt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]
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2021-07-12 fan mount broke sub 5 minutes, make thicker
    [[a]_xy_carriage_fan_mount_1_x1_rev3.STL, [a]_xy_carriage_fan_mount_2_x1_rev3.stl]
2021-07-18 fix hole size (now 6mm) on tall motor xy tower
    [tall_motor_short_idler_mount_12mm_belts_x2_rev4.STL]
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2021-08-30 fix missing set screw cutout in 2.1 z drive
    [[a]_40+20to1_z_drive_1_mirror_x2_rev1.STL, [a]_40+20to1_z_drive_1_x2_rev1.STL, [a]_40+20to1_z_drive_2_mirror_x2_rev1.STL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]
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2021-11-02 fix electronics brackets hole alignment
    [[a]_universal_controller_mounting_bracket_b_x2_rev1.STL, [a]_universal_rpi_mounting_bracket_b_x2_rev1.STL, universal_controller_mounting_bracket_a_x2_rev2.STL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]
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
